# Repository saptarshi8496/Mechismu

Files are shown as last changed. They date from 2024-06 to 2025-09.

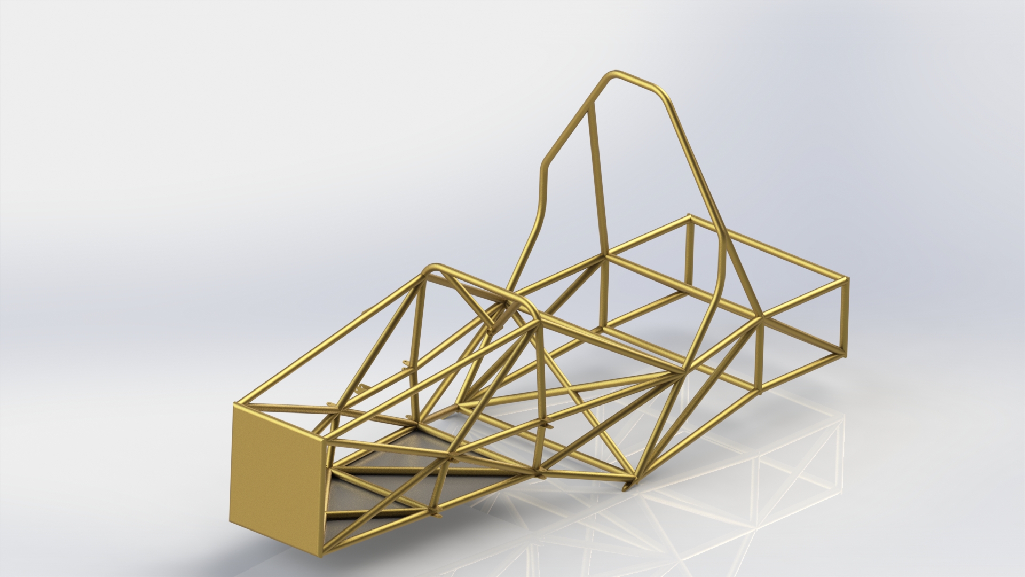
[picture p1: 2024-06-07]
Pictures/6.JPG

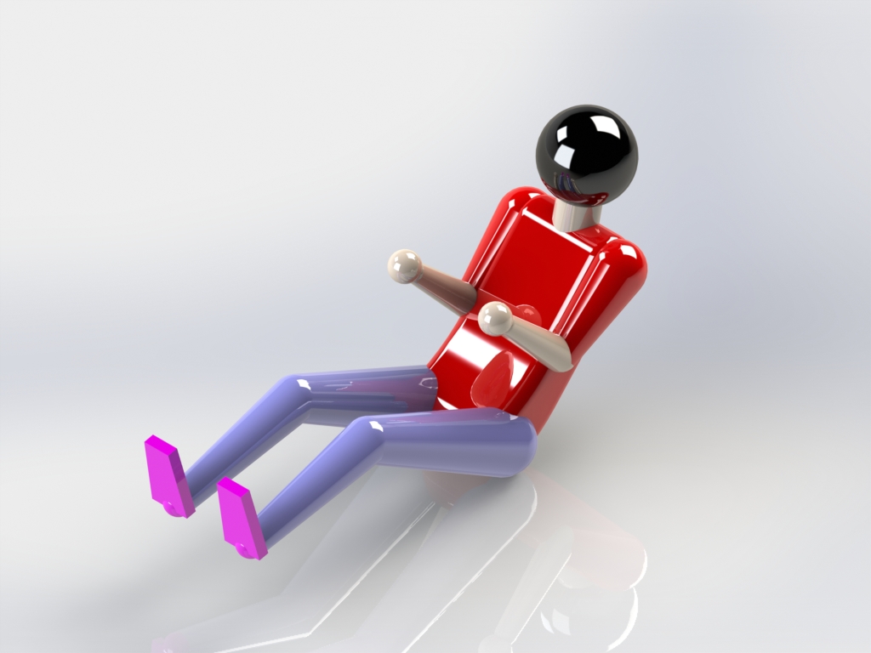
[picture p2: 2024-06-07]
Pictures/5.JPG

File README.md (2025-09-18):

# **Chassis Design & Fabrication – SolidWorks & ANSYS**

This project documents the complete process of design of a rule-compliant chassis for Formula Bharat 2025. The work focused on ensuring driver safety, manufacturability, and compliance with competition rules, while enabling integration with subsystems such as suspension, steering, and powertrain. An inside-to-outside approach was decided upon to design the chassis. This meant that we would start with the design of the powertrain system, such as the battery module, gearbox, motor placement etc. and then work on covering the area as efficiently as possible with the chassis.

## Table of Contents
- Introduction
- Project Workflow
- Key Features
- Softwares Used
- Results and Deliverables

### Material Selection

After careful consideration of the available materials on the basis of strength, cost, availability - we decided upon AISI 4130 (Chromoly Steel) as our material. This provided high strength and lower weight, but at a higher cost. However, it was readily available.

### Preparing the Outer Boundaries and Suspension Points

This was the first step in our design, as having a set 'box' to refer while making changes inside would make the design process simpler.

Three models were prepared - two templates for cockpit opening and cross-section, and one for Percy (95th Percentile Male). The rules regarding the cockpit templates were simple - they had to fit from the opening of the cockpit to a point below the side impact structures (for opening template) and to a point 100mm behind the rear face of brake pedals (for cross-section template). The models were created with dimensionns 10mm larger on each side in order to provide sufficient leeway for small alignment errors in the future.

The Percy model was used extensively to finalise the driver position for our car. In this, proper seat angle and side clearances for the drivers hands were measured and incorporated into the chassis design. This affected the height of the roll hoops and the distance from the front roll hoop to the front bulkhead. The height of the two roll hoops indirectly affected the angle as the top of the driver's helmet must be atleast 50mm from the line joining the top of the roll hoops. Also, the distance affected visibility - making it longer resulted in a more leaned driver.

### Preparing the Suspension Points

The suspension pick-up points were joined to the roll hoops and bulkheads in a star pattern to ensure maximum strength while keeping the design as simple as possible.

### Analysis

Impact analysis were carried out on the chassis to ensure safety. Three tests were performed - Impact (Front, Rear and Side), Bending and Torsion. These tests had different boundary conditions and forces applied, which were calculated considering an average case. The Factor of Safety obtained from these tests were taken as the ideal values. There would be loss in strength and stiffness after the chassis was built physically due to small misalignments, lack of perfect welding, certain dimensional errors and more.

### Trimming the Weldments and Creating Profiles

This was the most important part in terms of manufacturing. Proper trimming of all the joints were required in order to easily fit them after cutting the profiles. To prepare the chassis for this process, a colour code was followed to easily distinguish between tubes of three thicknesses - 2.5mm, 1.65mm and 1.2mm. After that, the process to convert the CAD Model to a physical model was as follows
1. Create a surface on each weldment with surface offset 0.
2. Flatten the surface separately by creating a very small slit.
3. Convert the flat surface to a drawing, and then print the PDF.
4. Paste the profile on tubes at proper lengths, and then cut the profiles.
5. Use fixtures designed earlier to align the tubes on a table.
6. Weld the joints and paint the chassis quickly to avoid rusting.

### Finalizing other components

After the key work of chassis design was completed, we proceded to the other departments' work. Mounts were designed and manufactured for all components - from suspension and brake pedals to battery and motor. 

### Documentation

To validate our

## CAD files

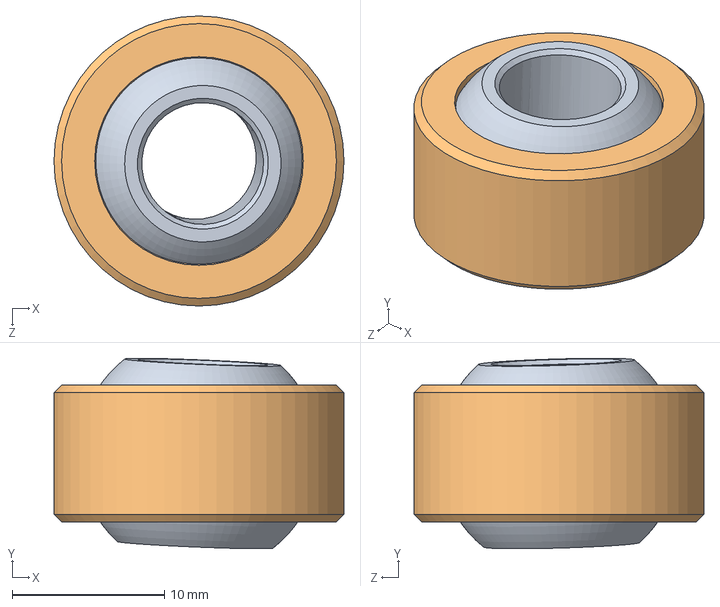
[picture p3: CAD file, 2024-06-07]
Parts/M8Spherical.SLDASM
19.1 x 12.5 x 19.1 mm
SPHolder
SPBall

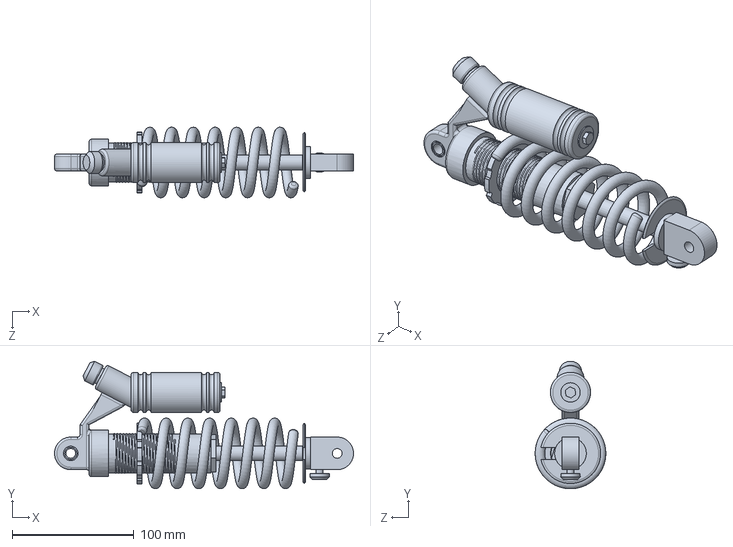
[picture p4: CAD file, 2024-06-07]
Parts/dnmStatic.SLDPRT
245.3 x 104.6 x 58.0 mm

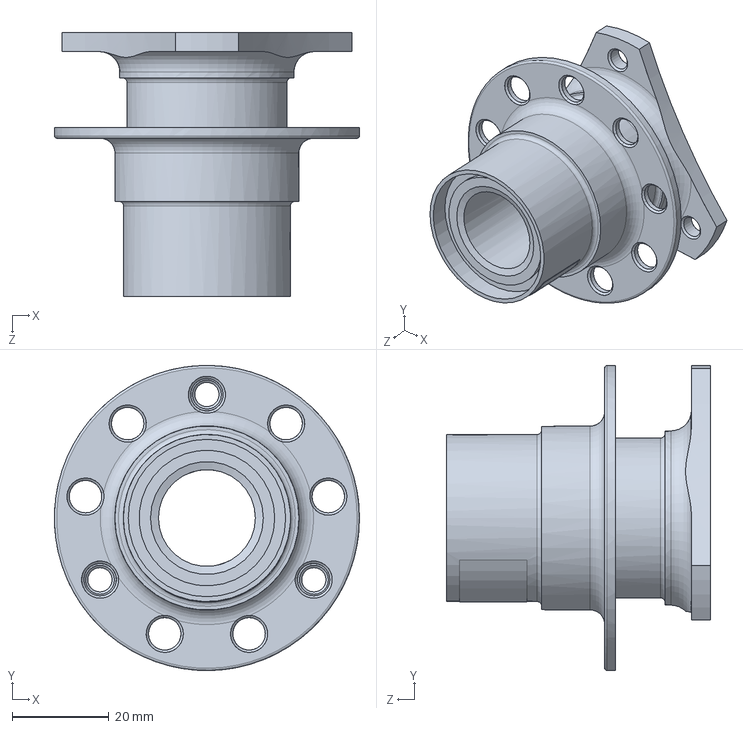
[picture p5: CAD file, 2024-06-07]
Parts/quick_release_mechanismsld.SLDPRT
63.0 x 63.0 x 54.6 mm

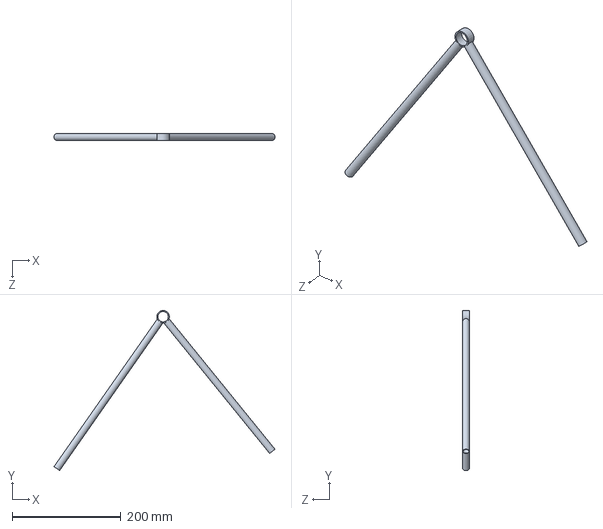
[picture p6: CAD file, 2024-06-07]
Parts/LowerArm.SLDPRT
406.6 x 294.5 x 12.7 mm

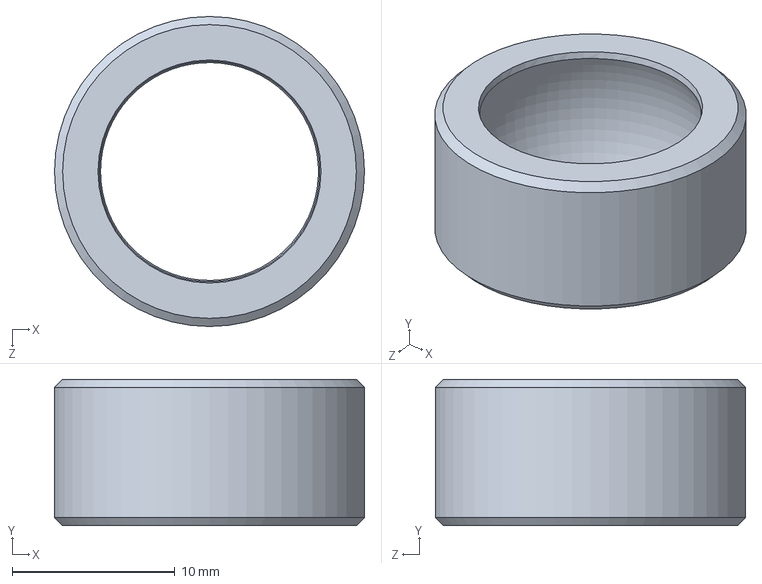
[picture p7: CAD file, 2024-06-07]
Parts/SPHolder.SLDPRT
19.1 x 9.00 x 19.1 mm

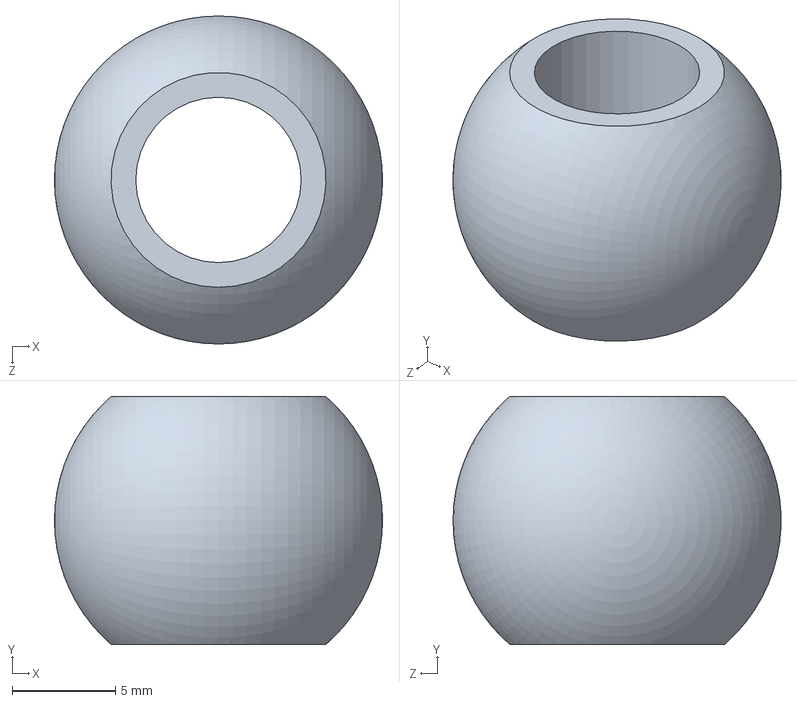
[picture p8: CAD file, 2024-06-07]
Parts/Ball.SLDPRT
15.9 x 12.0 x 15.9 mm

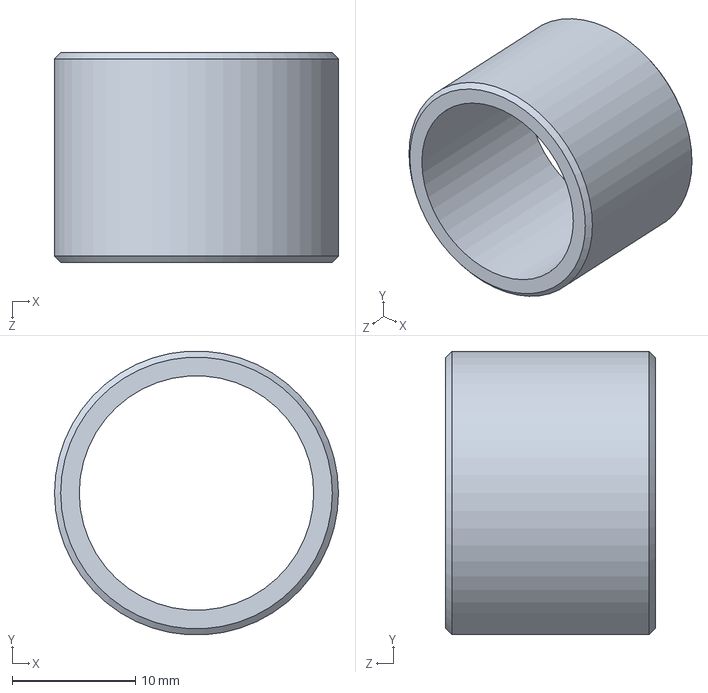
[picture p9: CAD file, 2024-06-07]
Parts/SCBearing.SLDPRT
23.0 x 23.0 x 17.0 mm

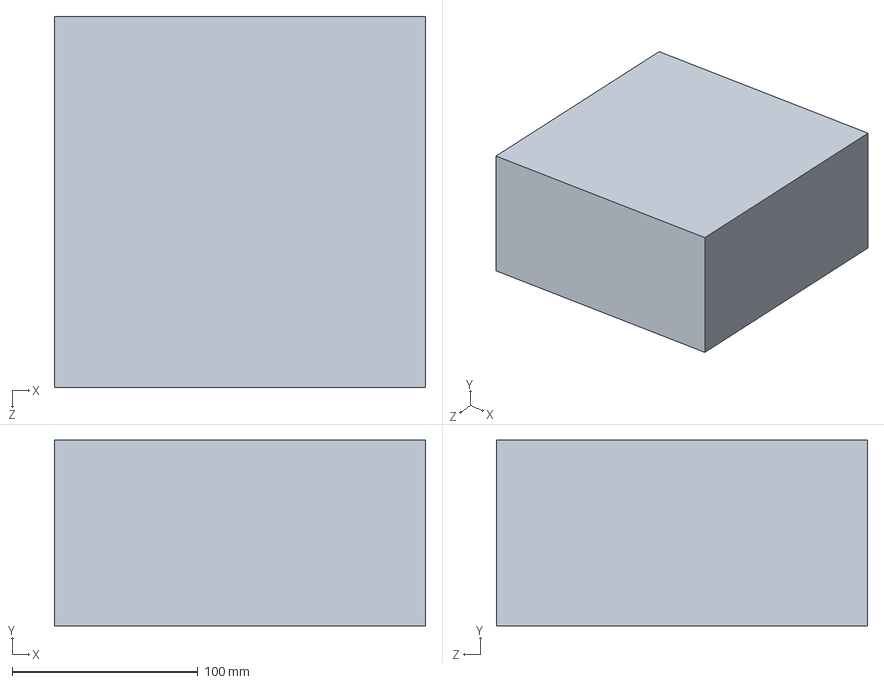
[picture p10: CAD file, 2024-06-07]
Parts/IAMin.SLDPRT
200.0 x 100.0 x 200.0 mm

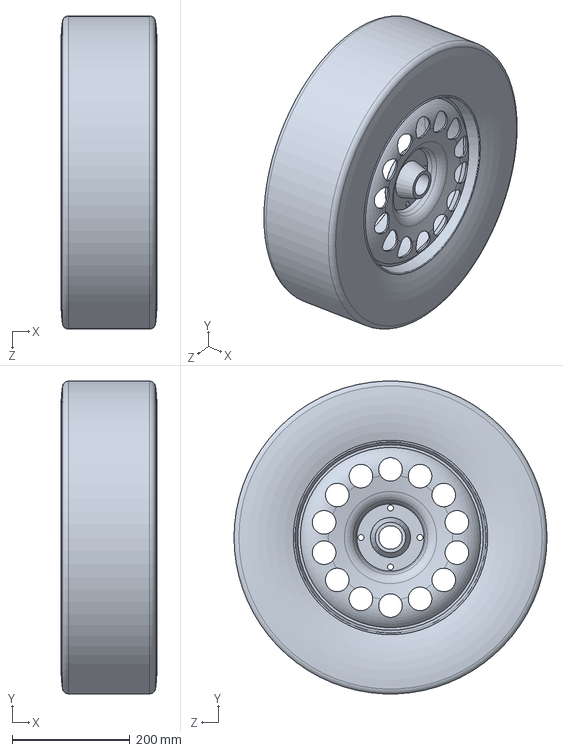
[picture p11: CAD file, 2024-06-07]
Parts/Wheels.SLDPRT
162.8 x 531.2 x 531.7 mm

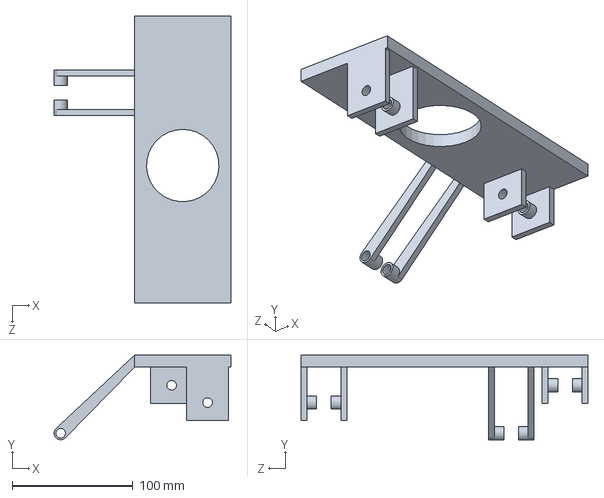
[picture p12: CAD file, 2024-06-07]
Parts/WheelHub.SLDPRT
146.7 x 70.2 x 238.0 mm

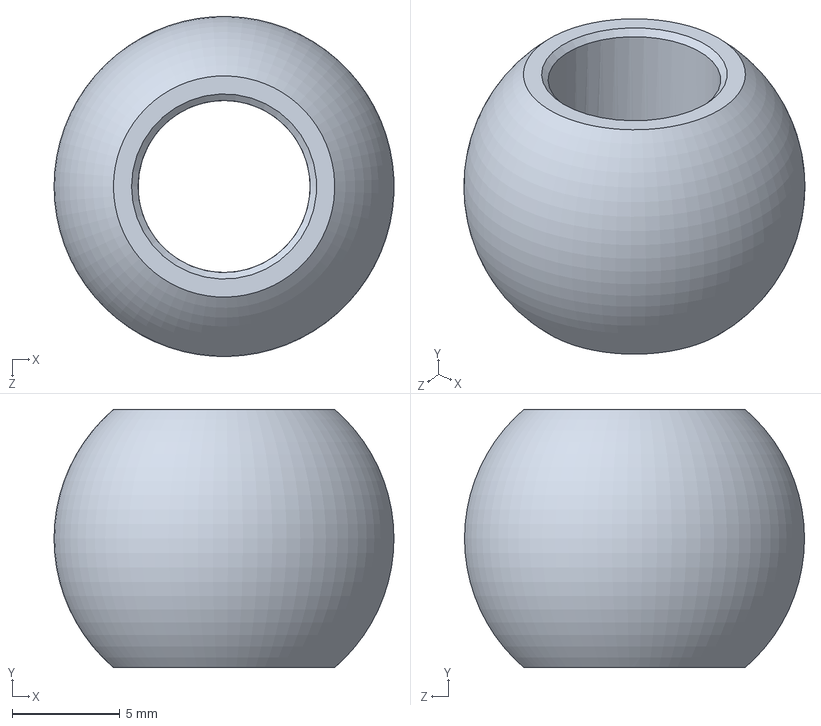
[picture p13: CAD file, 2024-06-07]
Parts/SPBall.SLDPRT
15.8 x 12.0 x 15.8 mm

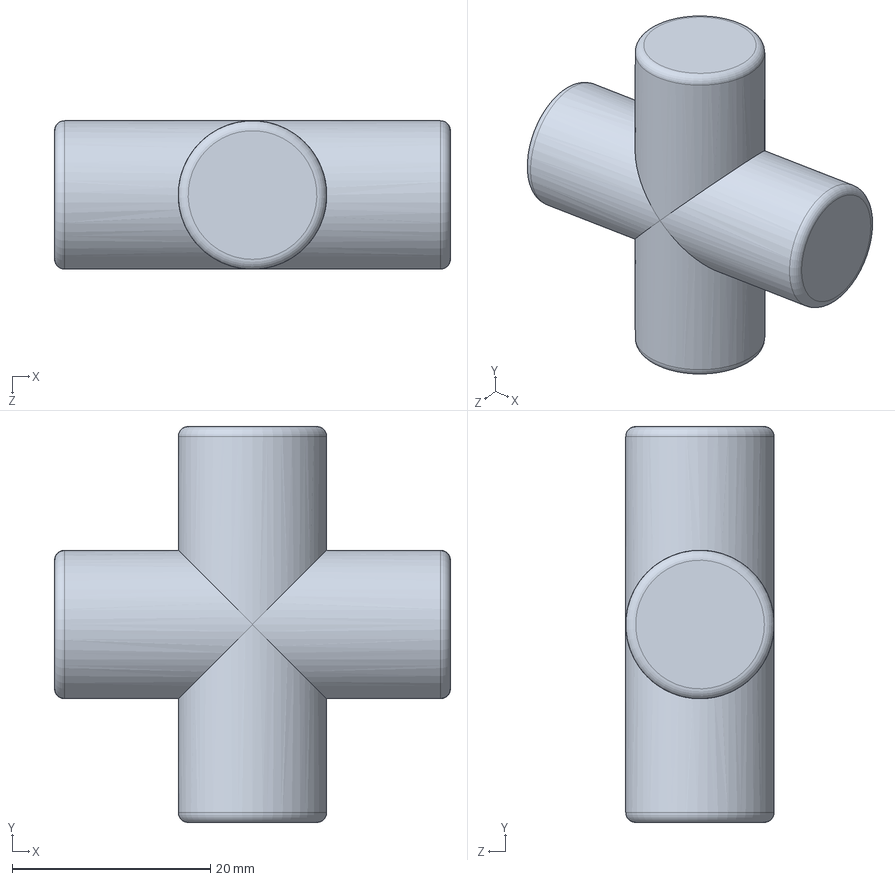
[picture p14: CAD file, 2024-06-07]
Parts/CROSS.SLDPRT
40.0 x 40.0 x 15.0 mm

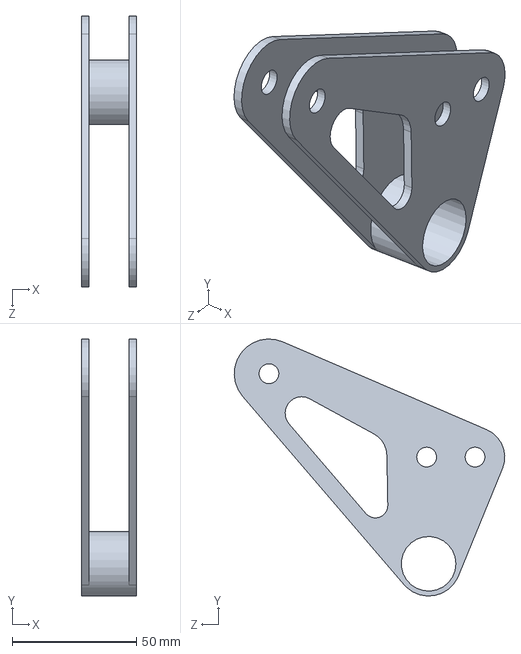
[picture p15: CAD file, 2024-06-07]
Parts/Rocker.SLDPRT
22.0 x 103.5 x 109.0 mm

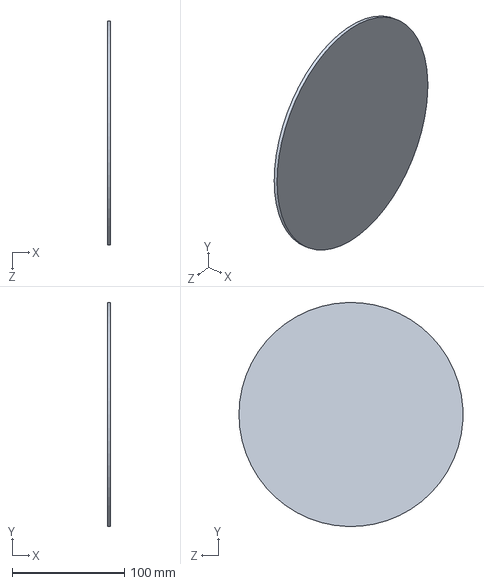
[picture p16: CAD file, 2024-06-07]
Parts/circle_200.SLDPRT
3.00 x 199.9 x 200.0 mm

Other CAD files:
Parts/percy.SLDASM
Parts/UVJ.SLDASM
Parts/ST1.SLDASM
Parts/M8RodEndSpacers.SLDPRT
Parts/3d_model_driver.SLDPRT
Parts/CET.SLDPRT
Parts/CST.SLDPRT
Parts/Chass1.SLDPRT
Parts/FW.SLDPRT
Parts/HeadRestrain.SLDPRT
Parts/Holder.SLDPRT
Parts/IA.SLDPRT
Parts/M8Spacer.SLDPRT
Parts/NoseConeFlat.SLDPRT
Parts/Pinion.SLDPRT
Parts/PullRod.SLDPRT
Parts/QRCoupling.SLDPRT
Parts/Seat.SLDPRT
Parts/Sketch.SLDPRT
Parts/SteeringRack.SLDPRT
Parts/SteeringWheel.SLDPRT
Parts/TieRod.SLDPRT
Parts/UpperArm.SLDPRT
Parts/YOKE.SLDPRT
Parts/head'.SLDPRT
Parts/line_280.SLDPRT
Parts/line_490.SLDPRT
Parts/line_915.SLDPRT
Parts/nosecone.SLDPRT
